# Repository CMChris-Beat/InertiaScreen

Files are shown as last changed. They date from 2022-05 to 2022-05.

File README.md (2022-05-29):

# Inertia Screen 惯性筛

**机电一体化课程设计—惯性筛**

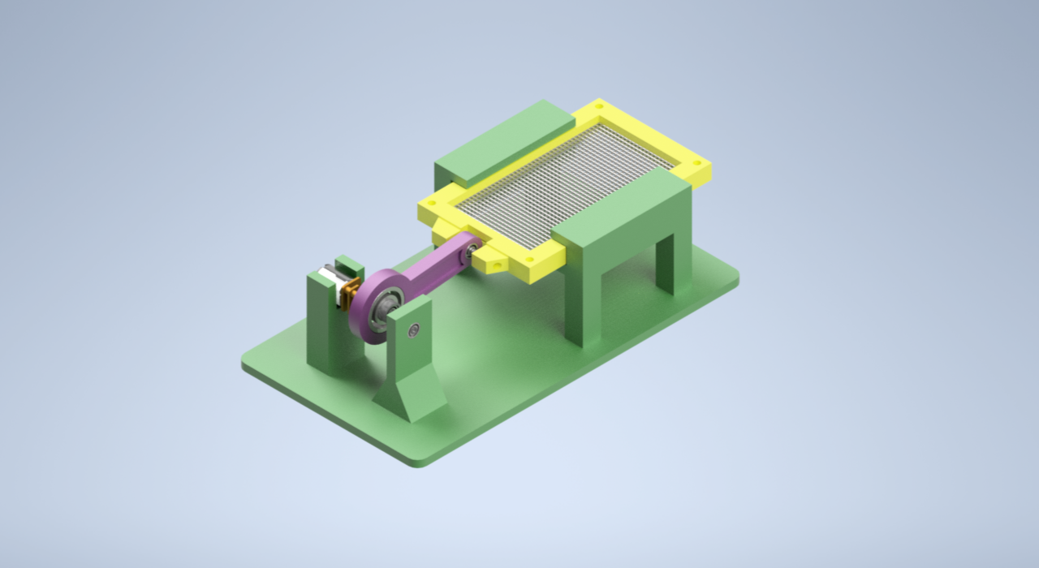
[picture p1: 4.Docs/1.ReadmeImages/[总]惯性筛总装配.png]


> 本项目是为了完成机电一体化课程设计而制作的，在参考了大量的机构后，选择了一个较容易实现且较为美观的设计——偏心轮机构。

另外，在制作完成后发现了一些问题也在这里列举一下：

* **惯性筛的筛动速度问题**，本着节省成本的想法，选用了3.3v~9v 出轴8mm的N20直流电机，但是在使用后一个很明显的问题就是速度，因为自己制作的电路板（V1版本，在更新V2版本的时候忘记备份了。。所以成本上去了，但是V2版本可以做循迹小车，可以遥控的那种）的缘故，电压最高只能给到5V，所以转速基本上是1圈/秒，室友看后直称“老奶奶筛”。˃̣̣̥᷄⌓˂̣̣̥᷅

* **惯性筛的稳定性及配合问题**，所有零件在安装完成后会与仿真图有很大出入，所以在安装的时候尽量保持零件之间的位置关系例如垂直及距离等，尤其是轴和轴配合的同心度也就是零件精度，会直接影响到后面运行时的稳定程度，**电机上方最好也压一下或者胶枪封一下，不然电机会上下跳动。**

* **偏心轮的偏心距问题**，为了制作尺寸小巧，偏心轮的偏心距很小，导致了惯性筛在筛动过程中的动作幅度很小，如果对筛动幅度有要求的化，可以自行加大零件尺寸进行修改。

* **急回特性问题**，本设计中采用的偏心轮可以等价为曲柄滑块机构，而**当偏心轮转动轴与筛网的水平移动轴不共线时，将会出现急回特性**，在本设计中没有考虑该问题，但因为偏心距较小所以急回不明显，但还是希望可以改进并消除该急回特性，保证惯性筛的筛动稳定。

* **惯性筛的效率问题**，制作的实物毕竟只是模型，在**实际筛料的过程中筛网应有一定的倾角**（15°至25°）会使得筛料在筛网上更好的运动，从而让惯性筛的效率提高。

* **零件的打印问题**，其余的都还好，机架长得~~太弯吧~~了，打印的时候加了不少支撑（支撑比模型还坚挺我是真的跪了orz，直接喜提战损版皮肤，~~胶枪粘~~），筛网下方区域是为了**预留空间给收集装置。**

* **一代电路板的问题**，开关的封装用错了导致后来的飞线，在最后我的实物展示图中可以看到，最大的问题是电路板的D7引脚，不知为何，在单独测试过程中输出正常，安装在电路板上时，无论输出高低电平，输出电压都为1.5V造成了很大的问题，我的解决方案是：因为这种结构的惯性筛并不需要正反转控制，所以直接**将D7飞线接地**，就解决了这个问题。

> 建模软件为Inventor而非SolidWorks，是因为我想要向Fusion 360及Inventor建模软件转的缘故，但是我都预留了转换好的Step模型方便大家使用。

> 关于课设要求交的各类文件，我都放在了4.Docs文件夹中，包括了仿真动画、说明书、答辩PPT和电路原理图等也方便大家参考。

---

### 电路部分

关于建模什么的我在这里就不多bb了，会的都会，不会的直接打印。(⁄ ⁄•⁄ω⁄•⁄ ⁄)

而关于电路和程序部分我需要单独讲一下，先是电路，由于操作失误一代也就是我现在使用的并没有保留下来但是原理图还是有的。**原理图中有部分错误已经在上文列出。**

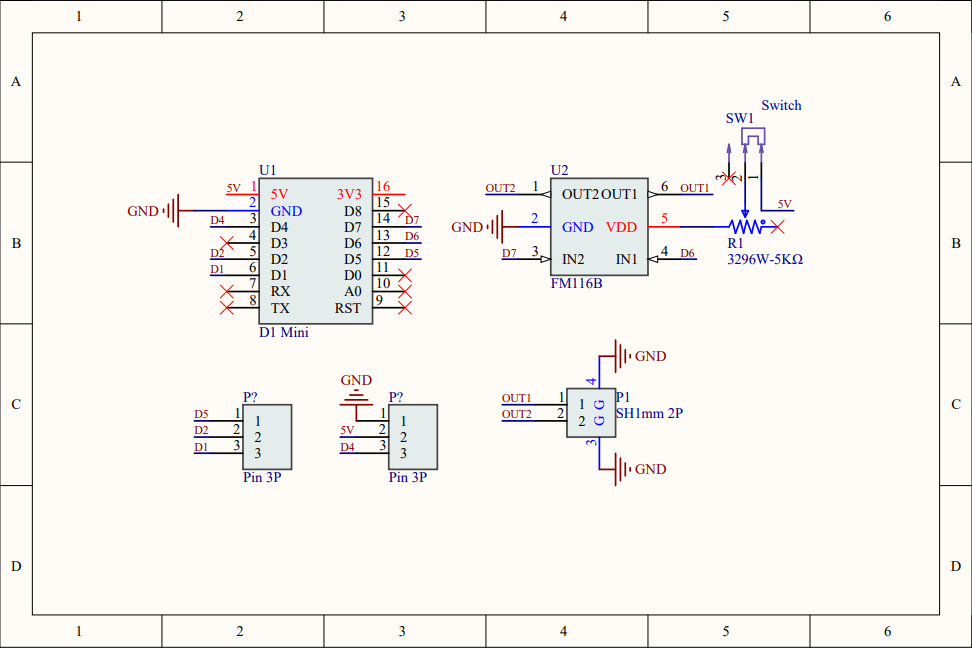
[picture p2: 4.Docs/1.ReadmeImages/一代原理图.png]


> 主要用到的元器件为（元器件皆可在淘宝店铺[优信电子](https://youxin-electronic.taobao.com/shop/view_shop.htm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)买到）：
>
> 1. D1 Mini 开发板（主控）
> 2. SH1.0mm 2P 的插头接口及对应单头线
> 3. FM116B 单路直流电机驱动器
> 4. 滑动变阻器（硬件调速使用）3296W-5KΩ
> 5. 贴片滑动开关
> 6. N20直流减速电机

二代图纸为改进版本，主要为了下学期的课设循迹小车准备的，在制作时同样会开源，可以在我的主页寻找，该电路可以使循迹小车还拥有遥控模式，同样采用N20，运转速度慢，但可以作为小玩具在答辩后玩。

具体的电路元器件需要什么我就不在这里列举了，感兴趣的可以下载后查看。

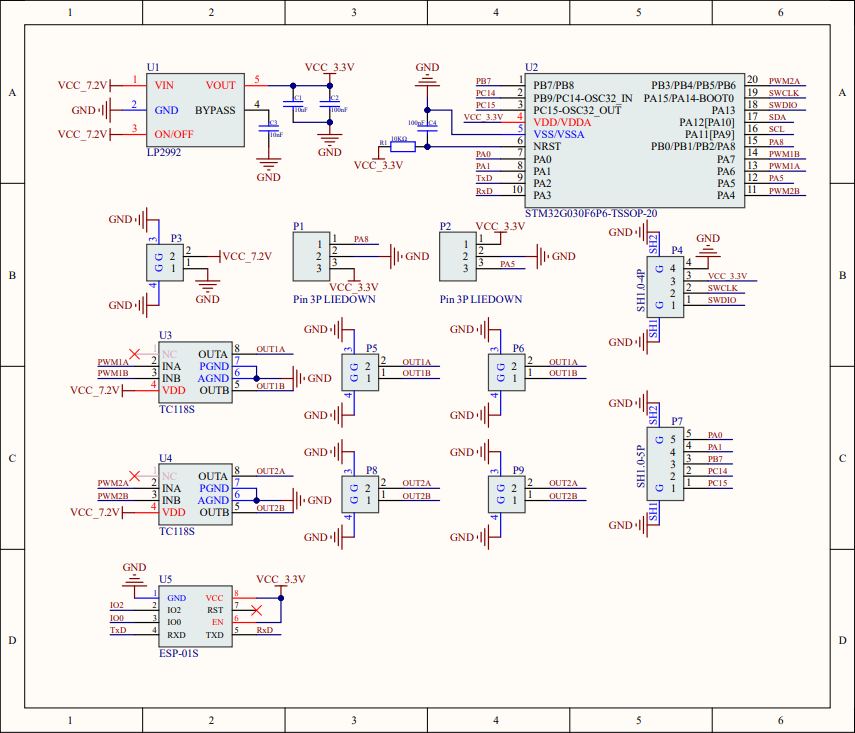
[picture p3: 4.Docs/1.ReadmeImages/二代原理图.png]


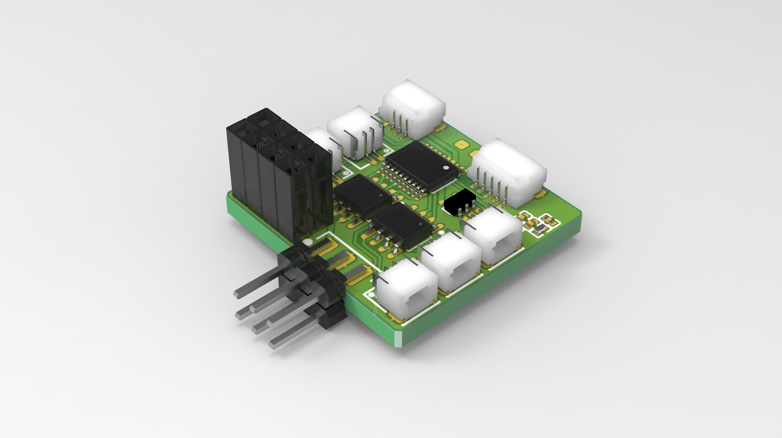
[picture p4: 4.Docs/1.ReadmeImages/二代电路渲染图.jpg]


### 程序部分

程序方面，使用的是Arduino，环境使用的Visual Studio平台下的Visual Micro，也可以使用VS Code的PlatformIO进行开发。

在代码中加入了Blinker库，用于远程手机控制（**点灯Blinker APP**），**要注意将密钥及Wifi等设置为自己的。**

**有能力的小伙伴可以将速度变快变慢的按钮换成滑块，能更好的控制速度，会丝滑很多。**

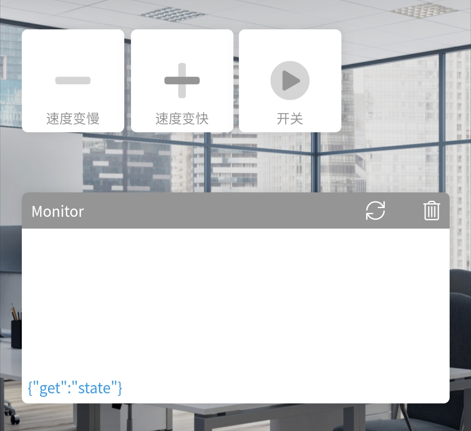
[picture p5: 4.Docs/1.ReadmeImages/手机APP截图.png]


### 实物展示

下面放一下我做好的实物图：



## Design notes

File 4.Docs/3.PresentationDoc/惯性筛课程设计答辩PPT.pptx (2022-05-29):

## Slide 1

机电一体化课程设计
惯性筛

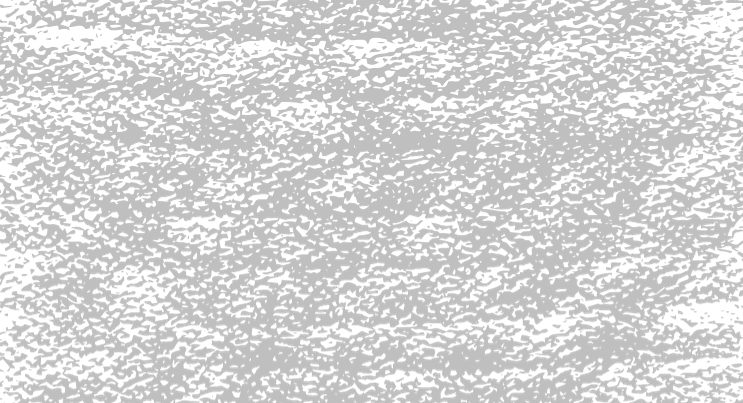
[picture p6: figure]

Course design of Mechatronics—Inertia screen

汇报人：ZHC

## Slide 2

目录
Contents

03.单击文本框输入标题
04.单击文本框输入标题

01.题目分析
02.单击文本框输入标题

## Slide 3

Topic analysis

壹

题目分析

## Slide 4

· 惯性筛是利用物体在没有受到外界作用力下保持静止状态或匀速直线运动状态的性质，来分离不同大小的物体。
· 惯性筛的传动轴在电动机的带动下高速旋转，轴上的圆盘及配重物在旋转过程中产生较大的惯性力，筛子在惯性力的作用下高速来回运动，将中、小物料进行筛分。

工作原理

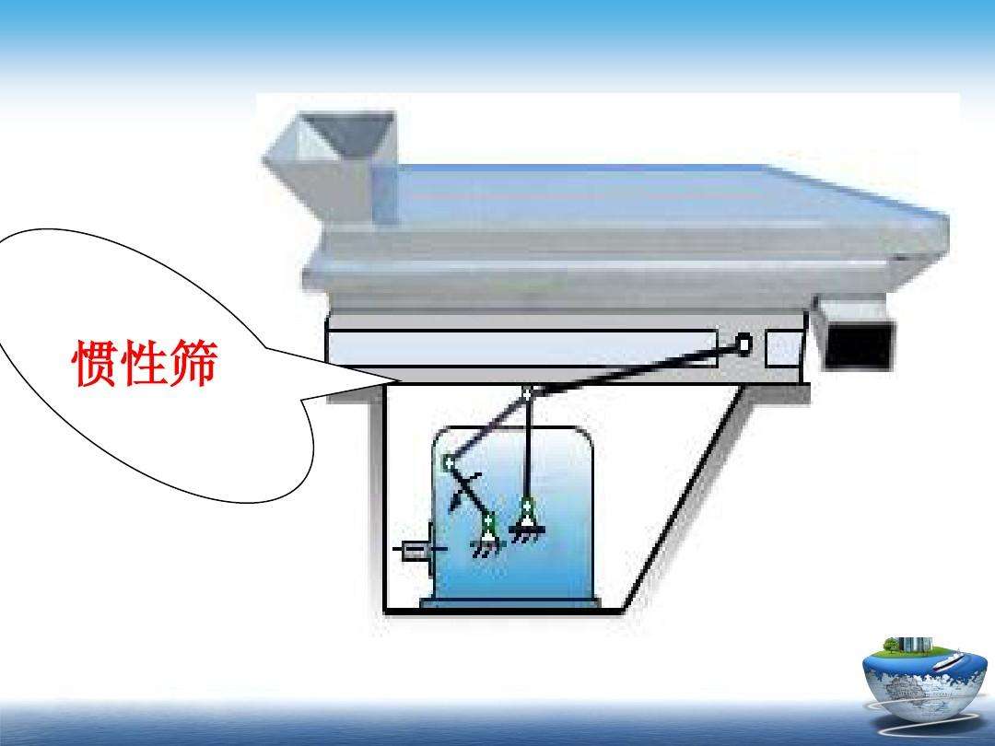
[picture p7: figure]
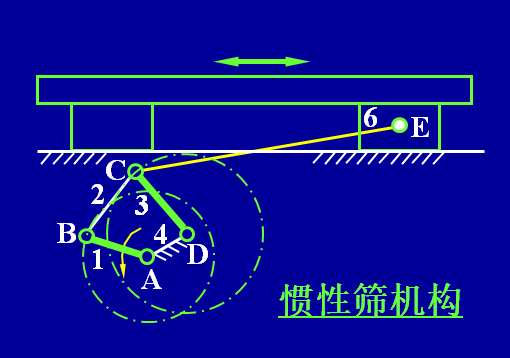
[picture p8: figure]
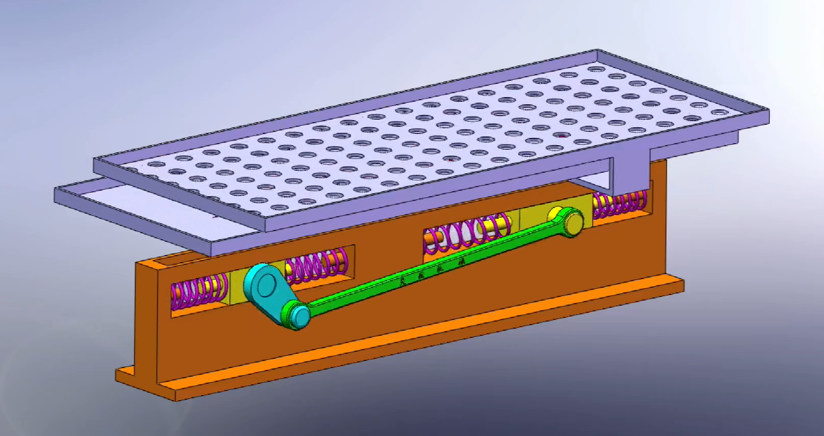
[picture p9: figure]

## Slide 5

传动方案对比

由曲柄和滑块的组合来实现转动和移动相互转换

以曲柄为主动件，把整周转动转换为往复移动

优点：设置为偏置曲柄滑块则具有急回特性

缺点：体积较大

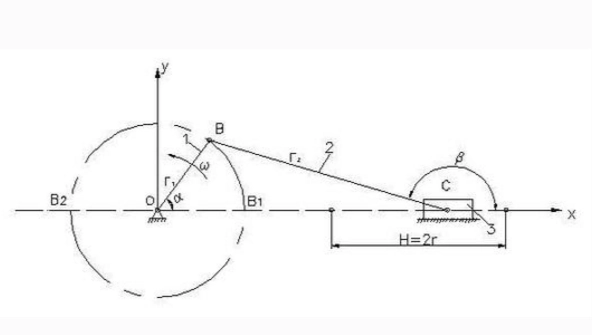
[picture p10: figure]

由凸轮，从动件和机架三个基本构件组成的高副机构

凸轮的轮廓线或凹槽的形状，可将连续的旋转运动转
化为往复的直线运动

优点：运动轨迹可以自行定制

缺点：制造复杂

曲柄滑块机构制作难度中等，采取偏置方式具有急回特性，可以提高运行效率，采取双曲柄带动滑块的方式可以使运行更加简便，也利于安装。

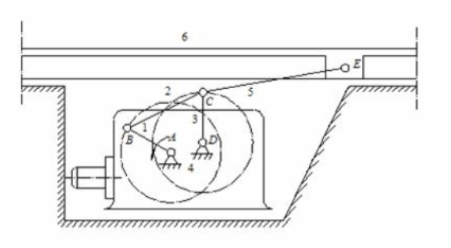
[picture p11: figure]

04
曲柄滑块

02
凸轮机构

03
偏置双曲柄
滑块

01
曲柄摇杆

由一个曲柄和一个摇杆组成的铰链四杆机构

曲柄为主动件且等速转动，而摇杆为从动件作变速往返摆动

优点：制作简单

缺点：输出轨迹不好确定

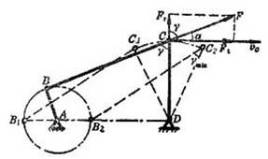
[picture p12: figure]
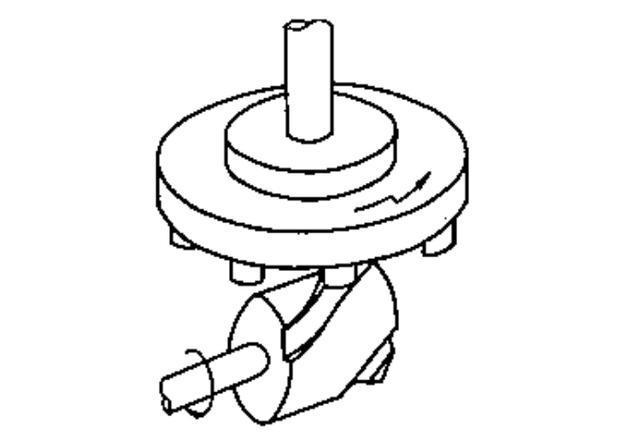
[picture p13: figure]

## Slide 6

传动方案的选择

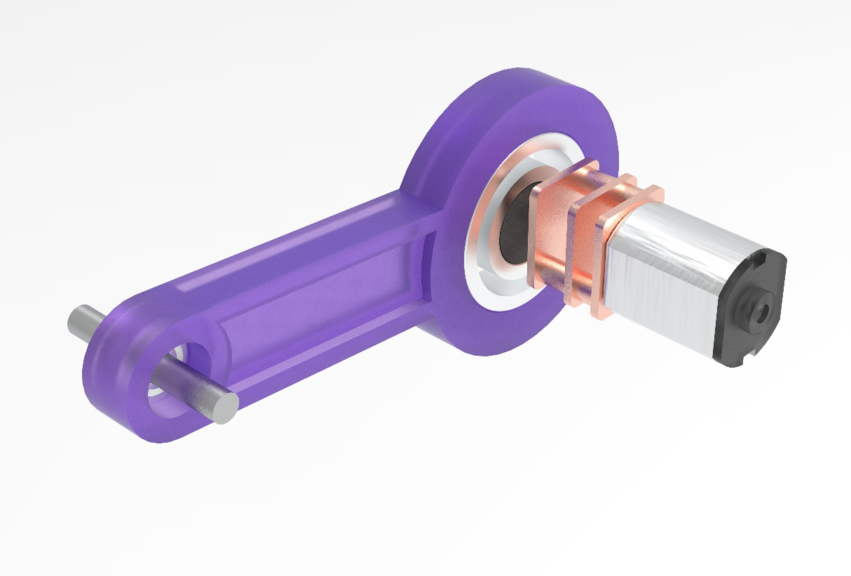
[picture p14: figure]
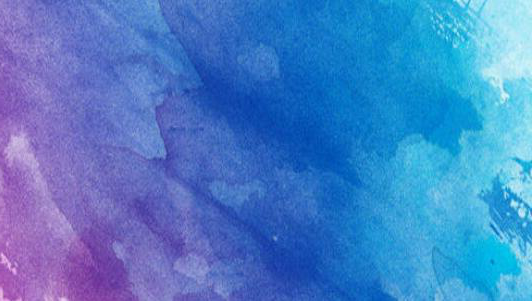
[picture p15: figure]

为了方便制作及体积要小，采用较为简单的结构，曲柄滑块机构，但是两个连杆如果不能保持平面度则不稳定。

使用偏心轮机构将机构简化，增加稳定性的同时，可以使结构变得更加紧凑。

偏心轮机构也有很多形式，为了最简化制作，只是将孔做在一侧，并未使用嵌套形式的偏心轮，固然会损失一部分稳定，但对于模型已经够用了。

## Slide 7

Circuit Design

贰

电路设计

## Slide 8

电路元器件的选择

电机

主控板

接线端子

因为模型较小，采用3D打印的形式进行制作，则电机负载较小，为了减小模型体积选用N20直流减速电机。

在项目初始就想加入联网功能，自然要选择ESP系列，又要求体积较小、好控制，所以选择了D1 Mini板。

为保证传输的稳定性及小型化，采用SH1.0mm封装的端子和插口线。

惯性筛只需要一个电机，为了小型化模型，筛选后采用FM116B单路直流电机驱动芯片进行驱动，成本只有0.7元。

电机驱动

除了能够联网控制外，我们还希望能够通过硬件进行控制，加入了滑动变阻器进行分压调速。

滑动变阻器

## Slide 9

· 电路首先要满足控制需求，由单片机两个IO口对电机驱动FM116B进行控制，因为对转速有调节需求，所以在IO选择上要选择可以输出PWM信号的IO。
· 其次对于滑动变阻器的分压，要注意在电路中的位置，其分压应与驱动芯片进行分压，电机内无电阻，如果在输出端进行分压，则无论阻值大小，所有电压都将由滑动变阻器承担，会导致电机无法转动。
· 为避免后续加入新功能，引出可以使用的几个多余IO口及电源，方便调试。

电路设计

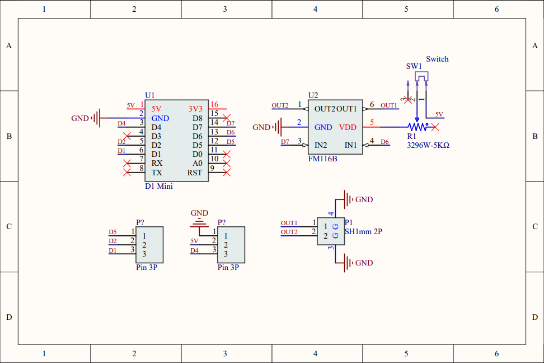
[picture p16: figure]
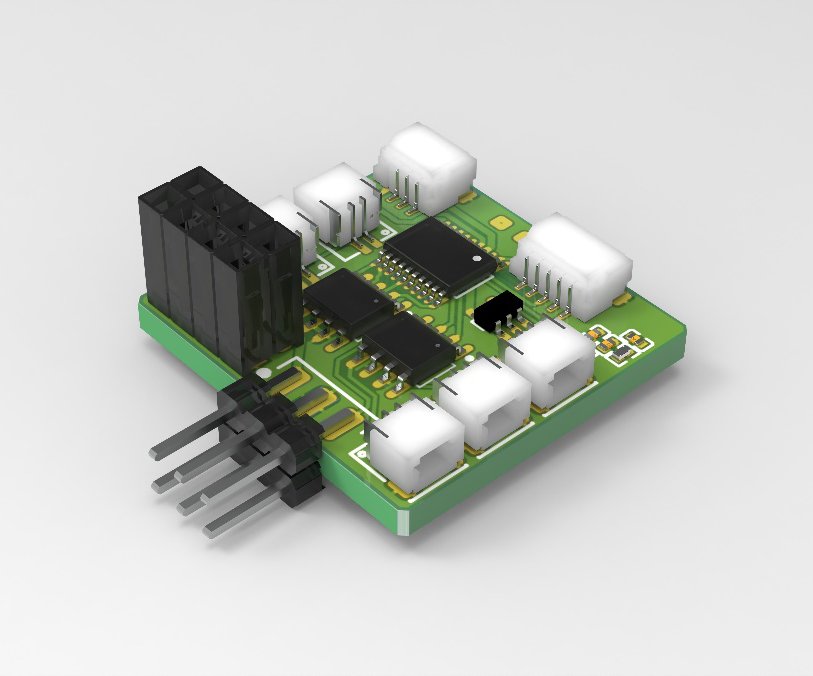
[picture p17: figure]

左上为设计的一代电路板，可以实现基础的功能，但是因为选型等问题出现了很多Bug，所以设计了左侧的二代电路板，加入了很多心得功能，并使其可以完成别的任务，不再局限于只有一个电机的情况。
并且由于一代板子对电机的驱动峰值只有4.6V左右，转速较慢，选用TC118S进行驱动，可以使电机驱动更加细腻。

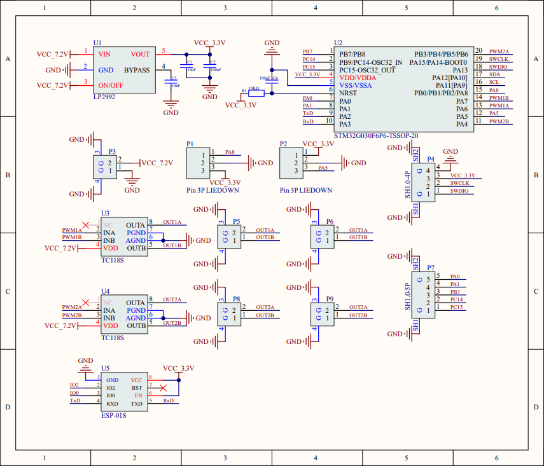
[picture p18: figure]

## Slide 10

Professional Generation Powerpoint

叁

单击文本框输入标题

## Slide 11

传动方案对比

单击编辑标题

单击此处可编辑内容，根据您的需要自由拉伸文本框大小

单击编辑标题

单击此处可编辑内容，根据您的需要自由拉伸文本框大小

单击编辑标题

单击此处可编辑内容，根据您的需要自由拉伸文本框大小

单击编辑标题

单击此处可编辑内容，根据您的需要自由拉伸文本框大小

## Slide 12

单击此处添加标题

单击编辑标题

单击此处可编辑内容，根据您的需要自由拉伸文本框大小

单击编辑标题

单击此处可编辑内容，根据您的需要自由拉伸文本框大小

单击编辑标题

单击此处可编辑内容，根据您的需要自由拉伸文本框大小

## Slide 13

单击此处添加标题

单击编辑标题

单击此处可编辑内容，根据您的需要自由拉伸文本框大小

单击编辑标题

单击此处可编辑内容，根据您的需要自由拉伸文本框大小

单击编辑标题

单击此处可编辑内容，根据您的需要自由拉伸文本框大小

单击编辑标题

单击此处可编辑内容，根据您的需要自由拉伸文本框大小

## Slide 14

单击此处编辑您要的内容，建议您在展示时采用微软雅黑字体，本模版所有图形线条及其相应素材均可自由编辑、改色、替换。更多使用说明和作品请详阅模版最末的使用手册。

单击此处添加标题

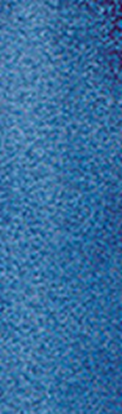
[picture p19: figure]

单击此处可编辑内容，根据您的需要自由拉伸文本框大小

01

单击此处可编辑内容，根据您的需要自由拉伸文本框大小

02

单击此处可编辑内容，根据您的需要自由拉伸文本框大小

03

单击此处可编辑内容，根据您的需要自由拉伸文本框大小

04

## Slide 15

单击此处添加标题

单击此处可编辑内容，根据您的需要自由拉伸文本框大小。单击此处可编辑内容，根据您的需要自由拉伸文本框大小。

关键词

单击此处可编辑内容

关键词

单击此处可编辑内容

关键词

单击此处可编辑内容

关键词

单击此处可编辑内容

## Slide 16

单击此处添加标题

单击编辑标题

单击此处可编辑内容，根据您的需要自由拉伸文本框大小

单击编辑标题

单击此处可编辑内容，根据您的需要自由拉伸文本框大小

单击编辑标题

单击此处可编辑内容，根据您的需要自由拉伸文本框大小

单击编辑标题

单击此处可编辑内容，根据您的需要自由拉伸文本框大小

单击编辑标题

单击此处可编辑内容，根据您的需要自由拉伸文本框大小

单击编辑标题

单击此处可编辑内容，根据您的需要自由拉伸文本框大小

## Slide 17

单击此处添加标题

关键词

1

单击此处编辑您要的内容，建议您在展示时采用微软雅黑字体。

关键词

2

单击此处编辑您要的内容，建议您在展示时采用微软雅黑字体。

关键词

单击此处编辑您要的内容，建议您在展示时采用微软雅黑字体。

3

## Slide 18

单击此处添加标题

单击编辑标题

单击此处可编辑内容，根据您的需要自由拉伸文本框大小

01

关键词

02

关键词

单击编辑标题

单击此处可编辑内容，根据您的需要自由拉伸文本框大小

03

关键词

04

关键词

单击编辑标题

单击此处可编辑内容，根据您的需要自由拉伸文本框大小

单击编辑标题

单击此处可编辑内容，根据您的需要自由拉伸文本框大小

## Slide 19

单击此处添加标题

单击此处可编辑内容，根据您的需要自由拉伸文本框大小

关键词

关键词

单击此处可编辑内容，根据您的需要自由拉伸文本框大小

单击此处可编辑内容，根据您的需要自由拉伸文本框大小

单击此处可编辑内容，根据您的需要自由拉伸文本框大小

关键词

关键词

单击此处可编辑内容，根据您的需要自由拉伸文本框大小

关键词

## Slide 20

单击此处添加标题

W
26%

S
85%

T
10%

O
45 %

单击编辑标题

单击此处可编辑内容，根据您的需要自由拉伸文本框大小

单击编辑标题

单击此处可编辑内容，根据您的需要自由拉伸文本框大小

单击编辑标题

单击此处可编辑内容，根据您的需要自由拉伸文本框大小

单击编辑标题

单击此处可编辑内容，根据您的需要自由拉伸文本框大小

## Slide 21

单击此处添加标题

单击此处可编辑内容，根据您的需要自由拉伸文本

单击此处可编辑内容，根据您的需要自由拉伸文本

关键词

关键词

关键词

单击此处可编辑内容，根据您的需要自由拉伸文本

单击此处可编辑内容，根据您的需要自由拉伸文本

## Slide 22

Professional Generation Powerpoint

肆

单击文本框输入标题

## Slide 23

单击此处添加标题

单击编辑标题

单击此处可编辑内容，根据您的需要自由拉伸文本框大小

单击编辑标题

单击此处可编辑内容，根据您的需要自由拉伸文本框大小

单击编辑标题

单击此处可编辑内容，根据您的需要自由拉伸文本框大小

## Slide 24

单击此处编辑您要的内容，建议您在展示时采用微软雅黑字体，本模版所有图形线条及其相应素材均可自由编辑、改色替换。更多使用说明和作品请详阅模版最末的使用手册。

单击此处添加标题

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
单击编辑标题

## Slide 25

单击此处添加标题

本模板的所有素材和逻辑图表，均可自由编辑替换和移动。

本模板的所有素材和逻辑图表，均可自由编辑替换和移动。

本模板的所有素材和逻辑图表，均可自由编辑替换和移动。

本模板的所有素材和逻辑图表，均可自由编辑替换和移动。

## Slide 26

单击此处添加标题

单击编辑标题

单击此处可编辑内容，根据您的需要自由拉伸文本框大小

单击编辑标题

单击此处可编辑内容，根据您的需要自由拉伸文本框大小

单击编辑标题

单击此处可编辑内容，根据您的需要自由拉伸文本框大小

单击编辑标题

单击此处可编辑内容，根据您的需要自由拉伸文本框大小

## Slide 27

THANK YOU

谢谢您的聆听

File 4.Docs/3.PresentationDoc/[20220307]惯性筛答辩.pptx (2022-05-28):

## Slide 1

惯性筛
课程设计

答辩人姓名

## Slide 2

CONTENTS

题目分析

01

工作原理及组成

02

传动方案对比与选择

03

总结

04

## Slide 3

01

题目分析

利用物体在没有受到外界作用力下保持静止状态或匀速直线运动状态的性质，来分离不同大小的物体。

体积大

筛网

惯性筛

体积小

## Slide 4


5、轴承
6、传动机构等

01

工作原理

惯性筛的传动轴在电动机的带动下高速旋转，轴上的圆盘及配重物在旋转过程中产生较大的惯性力，筛子在惯性力的作用下高速来回运动，将中、小物料进行筛分。

02

组成

1、筛箱
2、筛网
3、传动轴
4、电动机

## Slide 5

传动方案的对比与选择

曲柄滑块机构

曲柄摇杆机构

1

2

3

4

偏置双曲柄
滑块机构

凸轮机构

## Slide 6

传动方案的对比与选择


曲柄滑块机构

由曲柄和滑块的组合来实现转动和移动相互转换

以曲柄为主动件，把整周转动转换为往复移动

优点：设置为偏置曲柄滑块则具有急回特性

缺点：体积较大

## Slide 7

传动方案的对比与选择


凸轮机构

由凸轮，从动件和机架三个基本构件组成的高副机构

凸轮的轮廓线或凹槽的形状，可将连续的旋转运动转
化为往复的直线运动

优点：运动轨迹可以自行定制

缺点：制造复杂

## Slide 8

传动方案的对比与选择


曲柄摇杆机构

由一个曲柄和一个摇杆组成的铰链四杆机构

曲柄为主动件且等速转动，而摇杆为从动件作变速往返摆动

优点：制作简单

缺点：输出轨迹不好确定

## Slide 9

总结

偏置双曲柄滑块机构


曲柄滑块机构制作难度中等，采取偏置方式具有急回特性，可以提高运行效率，采取双曲柄带动滑块的方式可以使运行更加简便，也利于安装。

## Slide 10

THANKS

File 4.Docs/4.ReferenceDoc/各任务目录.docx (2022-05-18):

第八章 平面连杆机构及其设计.ppt

曲柄摇杆装置：

1) 曲柄摇杆机构
2) 曲柄摇杆1 、
3) 曲柄摇杆2 、
4) 双曲柄、
5) 双摇杆机构
6) 雷达天线俯仰机构 曲柄主动 曲柄摇杆机构演化

7）缝纫机踏板机构 摇杆主动

8）惯性筛机构 双曲柄机构演化

9）车门开闭机构 反平行四边形机构

10）汽车转向机构 等腰梯形机构 双摇杆机构

11）曲柄滑块机构

12) 小型刨床 导杆机构

13) 牛头刨床 导杆机构

14) 手摇唧筒

15) 正弦机构

16)圆盘锯

17）绕线机模型

18）对心直动滚子凸轮模型

19）内燃机气门机构模型

20）输送机模型

21）自动搬运小车

22）两级齿轮传动模型

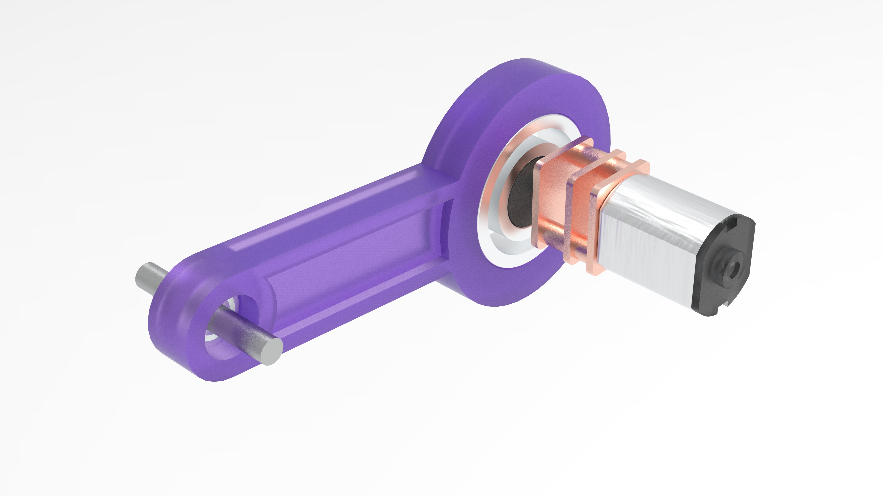
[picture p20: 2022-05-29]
4.Docs/1.ReadmeImages/偏心轮机构.jpg

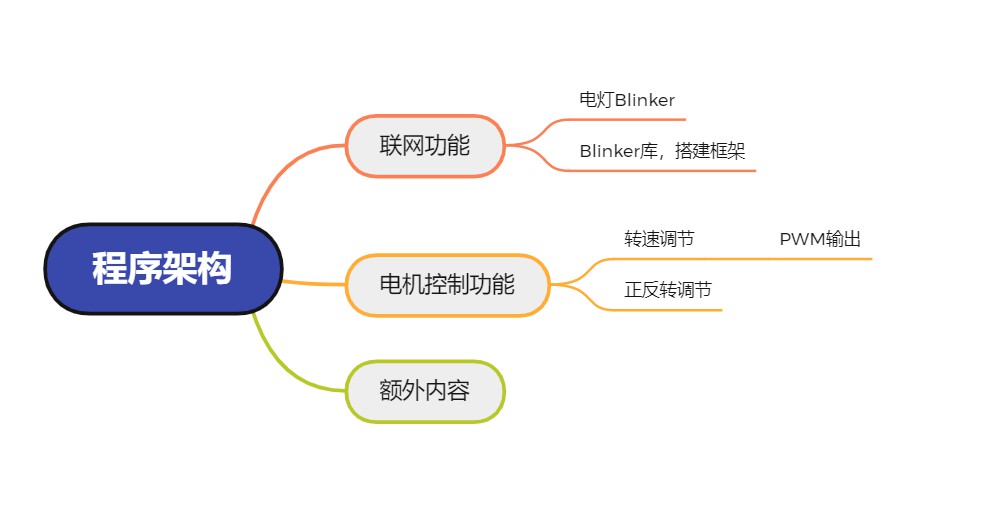
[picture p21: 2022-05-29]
4.Docs/1.ReadmeImages/程序框架.jpg

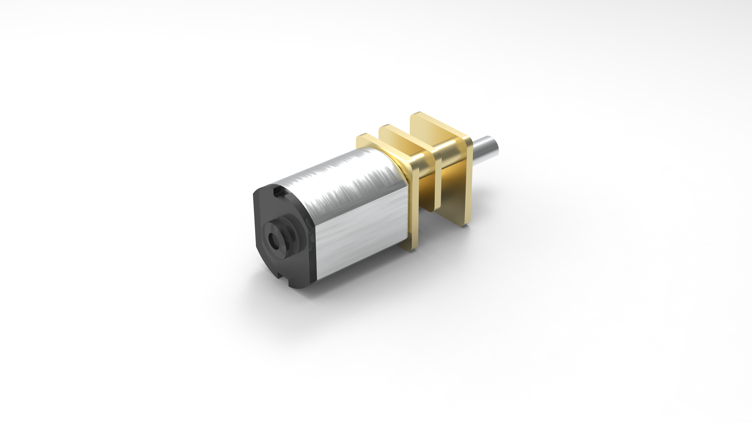
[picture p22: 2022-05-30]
4.Docs/1.ReadmeImages/N20电机渲染.jpg

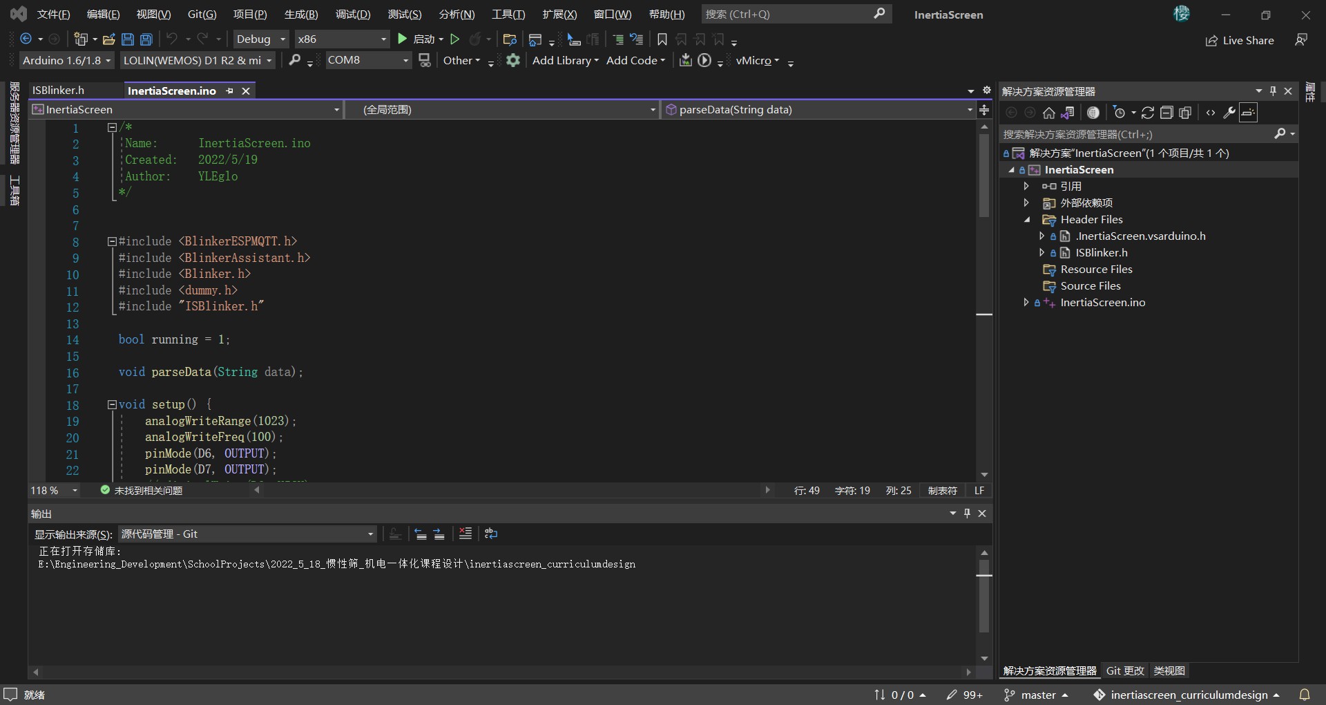
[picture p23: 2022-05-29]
4.Docs/1.ReadmeImages/程序截图.jpg

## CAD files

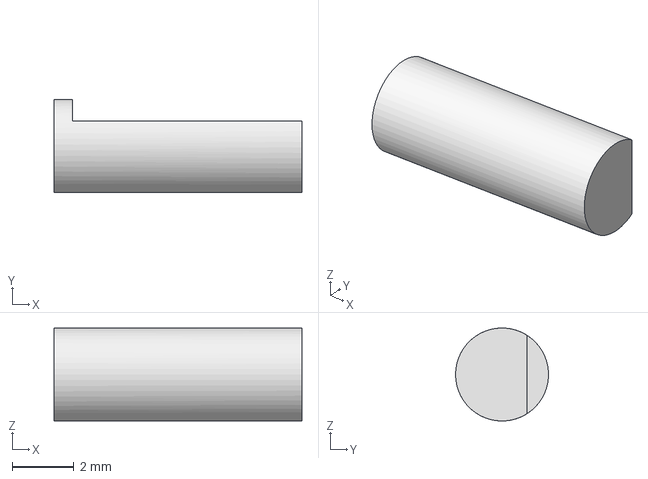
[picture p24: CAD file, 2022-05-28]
3.Model/2.3D_Simulation/Step/GA12-N20微型减速直流电机转动轴.stp
8.00 x 3.00 x 3.00 mm

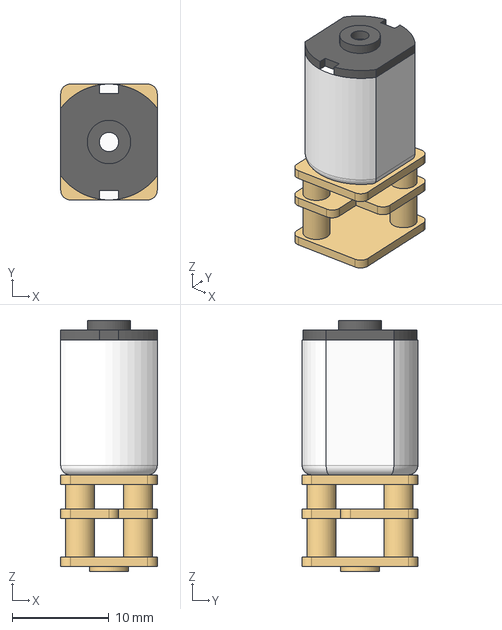
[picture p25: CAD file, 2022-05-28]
3.Model/2.3D_Simulation/Step/GA12-N20微型减速直流电机主机.stp
10.0 x 12.0 x 26.0 mm

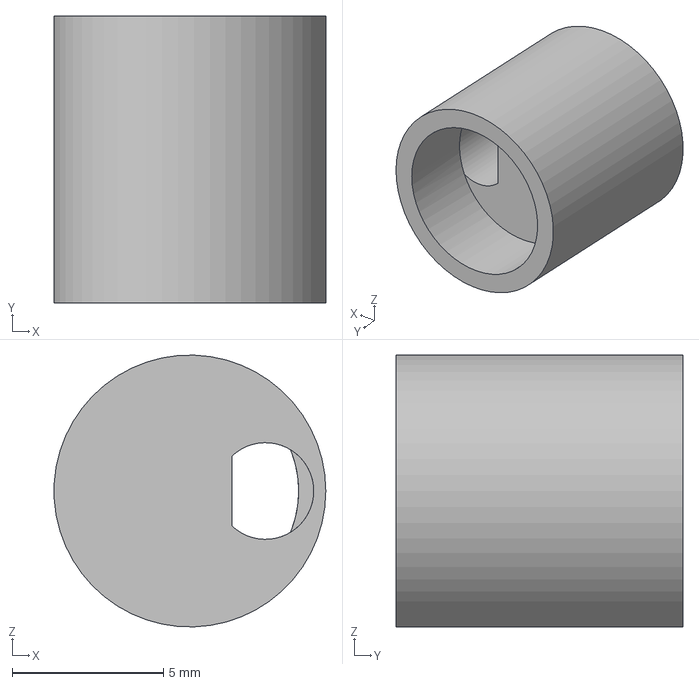
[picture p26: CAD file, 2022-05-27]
3.Model/2.3D_Simulation/Step/偏心轮.stp
8.99 x 9.50 x 9.00 mm

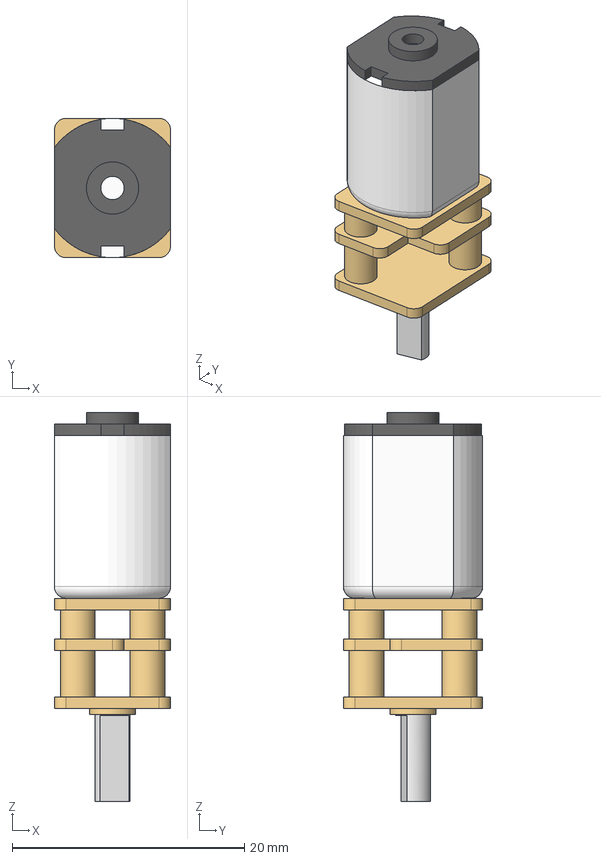
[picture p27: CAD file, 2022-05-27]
3.Model/2.3D_Simulation/Step/GA12-N20微型减速直流电机3V_15RPM_8mm.stp
10.0 x 12.0 x 33.5 mm
GA12-N20微型减速直流电机3V_15RP M
GA12-N20微型减速直流电机转动轴

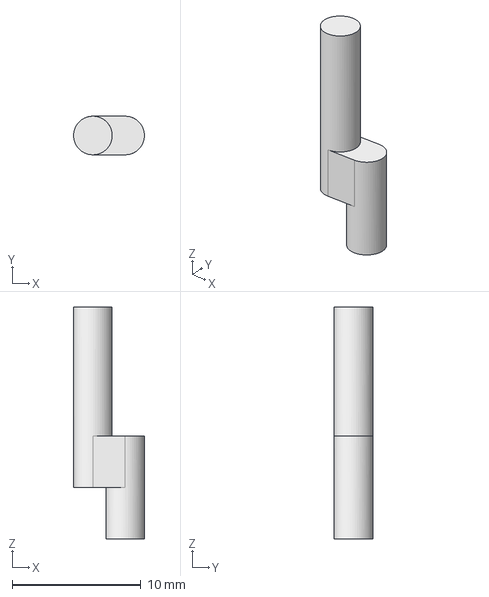
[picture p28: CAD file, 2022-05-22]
3.Model/2.3D_Simulation/Step/偏心支轴.stp
5.50 x 3.00 x 18.0 mm

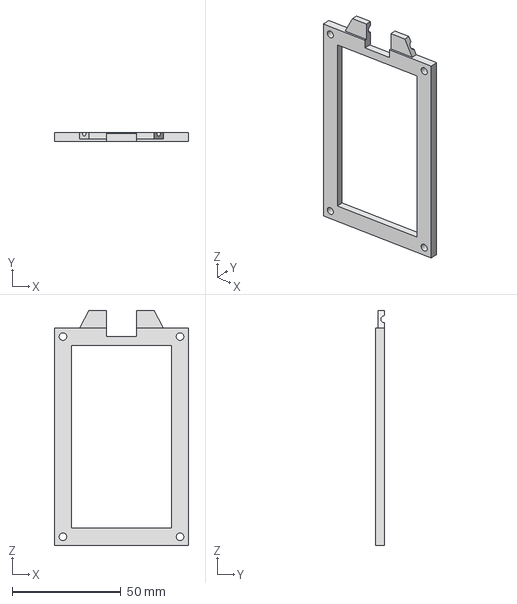
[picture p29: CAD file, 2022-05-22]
3.Model/2.3D_Simulation/Step/筛网上.stp
61.8 x 4.00 x 108.0 mm

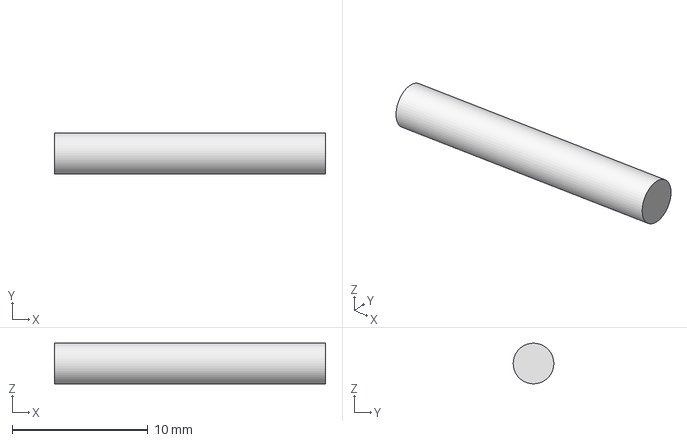
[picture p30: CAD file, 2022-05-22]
3.Model/2.3D_Simulation/Step/轴.stp
20.0 x 3.00 x 3.00 mm

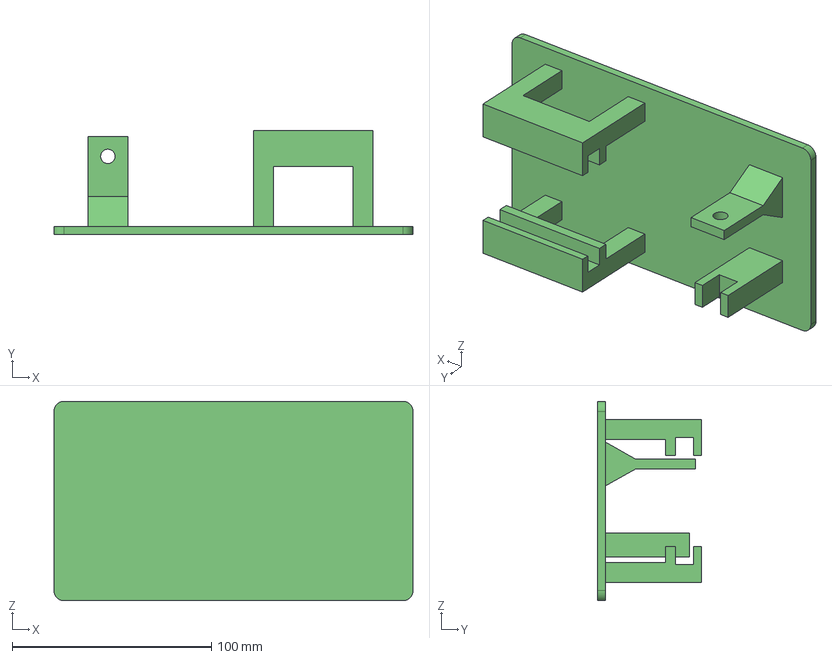
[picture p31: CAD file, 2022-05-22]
3.Model/2.3D_Simulation/Step/机架.stp
180.0 x 52.0 x 100.0 mm

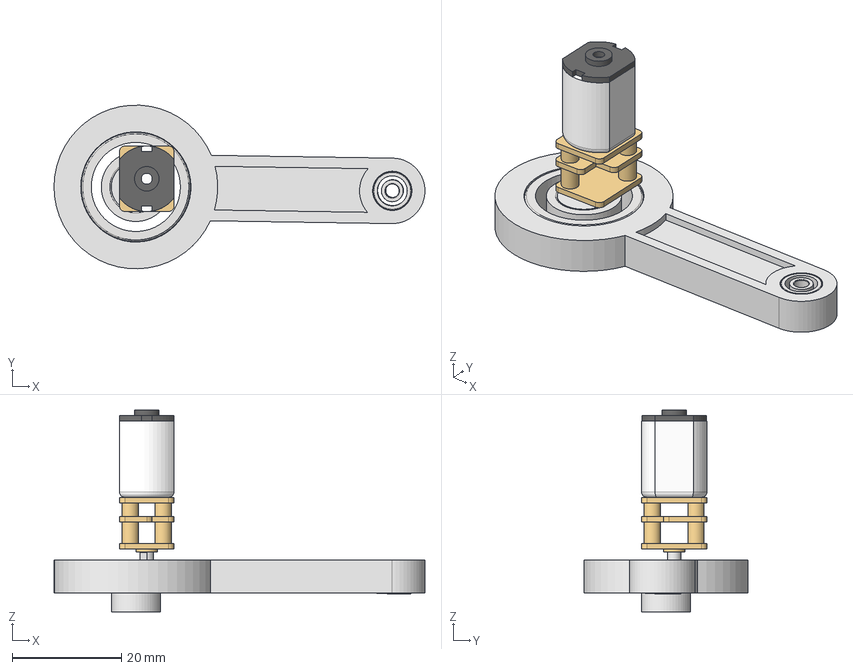
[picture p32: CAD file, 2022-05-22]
3.Model/2.3D_Simulation/Step/[装配]惯性筛偏心轮装配.stp
68.0 x 30.0 x 37.0 mm
GA12-N20微型减速直流电机3V_15RP M
GA12-N20微型减速直流电机转动轴
偏心轮
偏心轮外连接件
ISO 1224 - 38 3 x 7 x 3
ISO 1224 - 19 9 x 20 x 6
ISO 1224 - 19 2.5 x 7 x 2.5 x 2

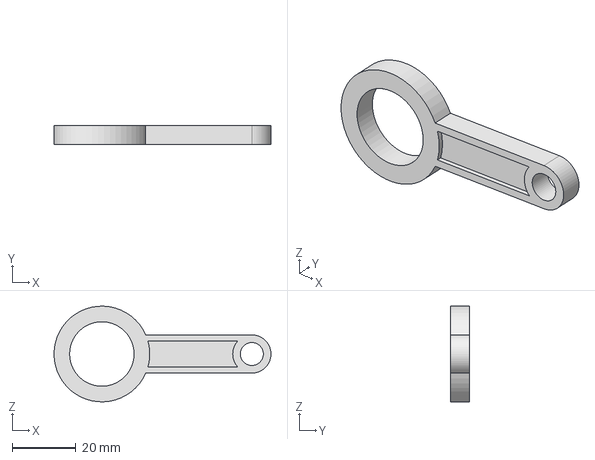
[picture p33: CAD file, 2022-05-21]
3.Model/2.3D_Simulation/Step/偏心轮外连接件.stp
68.0 x 6.00 x 30.0 mm

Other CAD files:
3.Model/1.Drawings/惯性筛装配图.dwg
3.Model/1.Drawings/筛网上.dwg
3.Model/1.Drawings/筛网下.dwg
3.Model/1.Drawings/偏心轮.dwg
3.Model/1.Drawings/偏心轮外连接件.dwg
3.Model/1.Drawings/机架.dwg
3.Model/1.Drawings/偏心支轴.dwg
3.Model/2.3D_Simulation/Step/筛网下.stp
3.Model/2.3D_Simulation/Ipt/1.偏心轮/GA12-N20微型减速直流电机3V_15RPM_8mm.iam
3.Model/2.3D_Simulation/Ipt/1.偏心轮/GA12-N20微型减速直流电机3V_15RPM_8mm.ipt
3.Model/2.3D_Simulation/Ipt/1.偏心轮/GA12-N20微型减速直流电机主机.ipt
3.Model/2.3D_Simulation/Ipt/1.偏心轮/GA12-N20微型减速直流电机转动轴.ipt
3.Model/2.3D_Simulation/Ipt/1.偏心轮/偏心支轴.ipt
3.Model/2.3D_Simulation/Ipt/1.偏心轮/偏心轮.ipt
3.Model/2.3D_Simulation/Ipt/1.偏心轮/偏心轮外连接件.ipt
3.Model/2.3D_Simulation/Ipt/2.轴承/BS 3469 - 19 - 2.5 x 7 x 2.5.ipt
3.Model/2.3D_Simulation/Ipt/2.轴承/ISO 1224 - 19 2.5 x 7 x 2.5.ipt
3.Model/2.3D_Simulation/Ipt/2.轴承/ISO 1224 - 19 9 x 20 x 6.ipt
3.Model/2.3D_Simulation/Ipt/2.轴承/ISO 1224 - 38 3 x 7 x 3.ipt
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

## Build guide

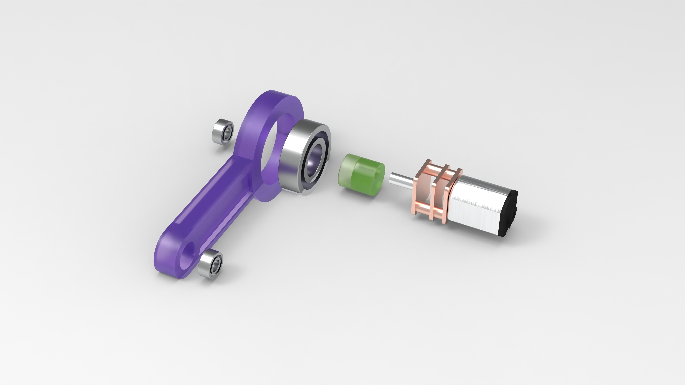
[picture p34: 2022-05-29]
4.Docs/1.ReadmeImages/偏心轮机构组装图.jpg

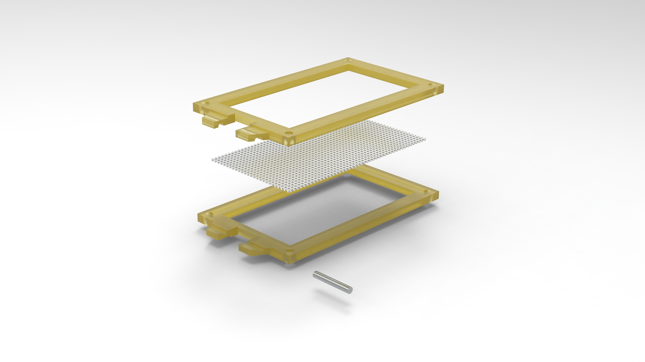
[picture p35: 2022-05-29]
4.Docs/1.ReadmeImages/筛网组装图.jpg

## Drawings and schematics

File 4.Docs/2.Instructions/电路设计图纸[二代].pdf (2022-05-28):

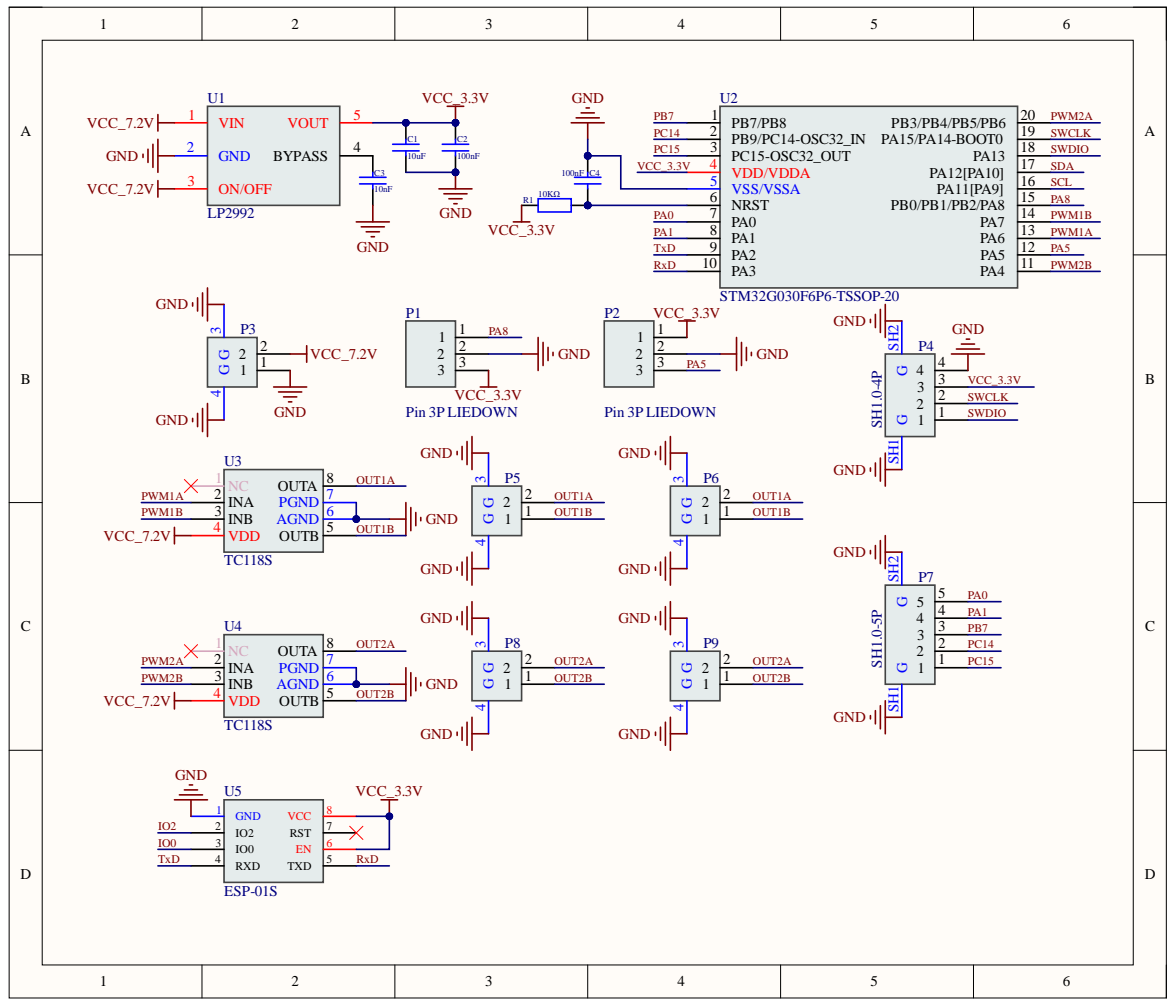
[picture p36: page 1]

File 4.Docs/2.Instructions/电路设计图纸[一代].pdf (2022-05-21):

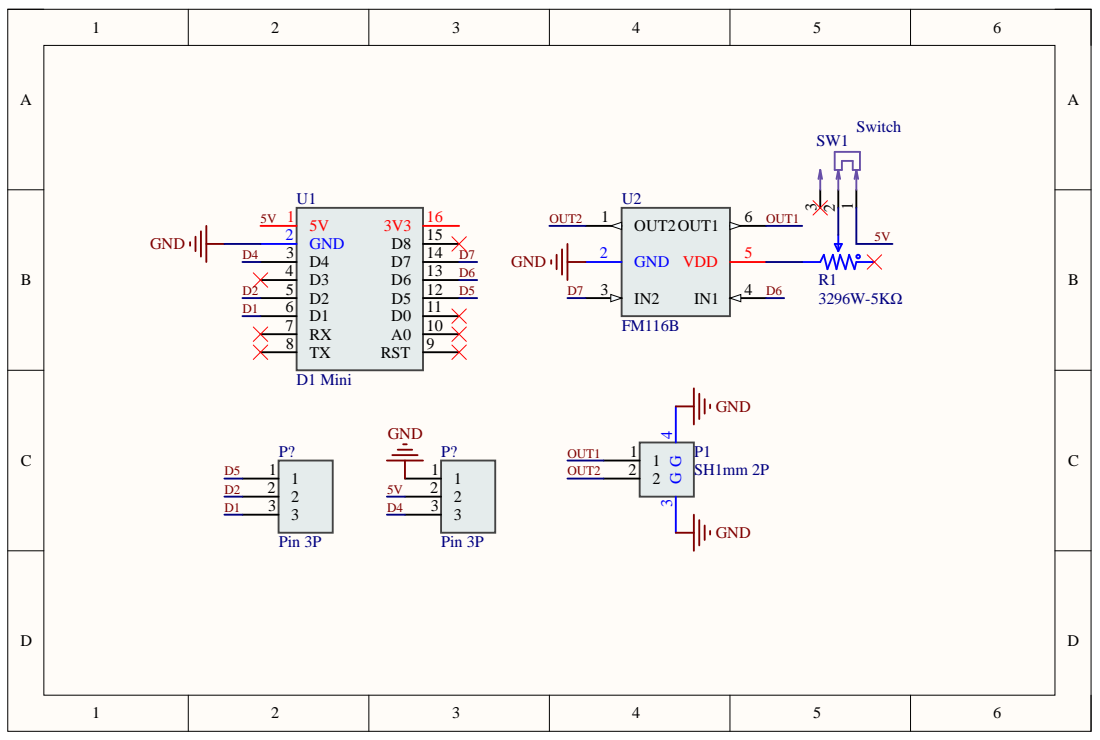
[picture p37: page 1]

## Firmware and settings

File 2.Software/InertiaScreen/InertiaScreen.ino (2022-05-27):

/*
 Name:		InertiaScreen.ino
 Created:	2022/5/19
 Author:	YLEglo
*/


#include <BlinkerESPMQTT.h>
#include <BlinkerAssistant.h>
#include <Blinker.h>
#include <dummy.h>
#include "ISBlinker.h"

bool running = 1;

void parseData(String data);

void setup() {
	analogWriteRange(1023);
	analogWriteFreq(100);
	pinMode(D6, OUTPUT);
	pinMode(D7, OUTPUT);
	// digitalWrite(D6, HIGH);
	analogWrite(D6, speed);
	digitalWrite(D7, LOW);
	BLINKER_DEBUG.stream(Serial);
	Blinker.begin(auth, ssid, pswd);
	Button1.attach(button1_callback);
	Button2.attach(button2_callback);
	Button3.attach(button3_callback);
}

void loop() {
	Blinker.run();
	parseData(input);
	if (running == 0) analogWrite(D6, 0);
	else analogWrite(D6, speed);
}

void parseData(String data) {
	switch (data.toInt()) {
		case 1: // Slow
			if (flag) {
				if (speed > 23) speed -= 100;
				Blinker.print("Speed: ", speed);
				flag = 0;
			}
			break;
		case 2: // Quick
			if (flag) {
				if (speed < 1023) speed += 100;
				Blinker.print("Speed: ", speed);
				flag = 0;
			}
			break;
		case 3: // Stop
			if (flag) {
				running = !running;
				Blinker.print("State: ", running);
				flag = 0;
			}
			break;
		default:
			running = 1;
			break;
	}
}

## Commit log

2022-05-18 [HW]Upload Hardware Project
    [InertiaScreen_CurriculumDesign.PcbDoc, InertiaScreen_CurriculumDesign.PrjPcb, InertiaScreen_CurriculumDesign.SchDoc]
2022-05-18 [Md]Upload part of Model
    [InertiaScreen_CurriculumDesign.SchDoc, 偏心轮.ipt]
2022-05-19 [SW]Upload Test Program
    [InertiaScreen_CurriculumDesign.PrjPcb, InertiaScreen_CurriculumDesign.SchDoc, 偏心轮.0001.ipt]
2022-05-20 [HW]Update Hardware
    [InertiaScreen_CurriculumDesign.PcbDoc, InertiaScreen_CurriculumDesign.SchDoc]
2022-05-21 [Docs]Upload Circuit Drawing
    [InertiaScreen_CurriculumDesign.PrjPcb, InertiaScreen_CurriculumDesign.SchDoc]
2022-05-21 [Md]Update Model, complete Eccentric mechanism
    [BS 3469 - 19 - 2.5 x 7 x 2.5.ipt, GA12-N20微型减速直流电机3V_15RPM_8mm.ipt, GA12-N20微型减速直流电机3V_15RPM_8mm.stp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]
2022-05-21 Organize documents
    [BS 3469 - 19 - 2.5 x 7 x 2.5.ipt, GA12-N20微型减速直流电机3V_15RPM_8mm.ipt, ISO 1224 - 19 2.5 x 7 x 2.5.ipt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]
2022-05-21 [Md]Update Model, only Rack left
    [GA12-N20微型减速直流电机3V_15RPM_8mm.iam, GA12-N20微型减速直流电机3V_15RPM_8mm.ipt, GA12-N20微型减速直流电机主机.ipt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]
2022-05-22 [Md]Complete Model making
    [GA12-N20微型减速直流电机3V_15RPM_8mm.iam, GA12-N20微型减速直流电机3V_15RPM_8mm.stp, [总]惯性筛总装配.iam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]
2022-05-22 [Md]Upload 2D drawing
    [[总]惯性筛总装配.iam, 偏心支轴.dwg, 偏心轮.dwg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]
2022-05-25 [HW]Update Hardware, Replace the switch package
    [InertiaScreen_CurriculumDesign.PcbDoc, InertiaScreen_CurriculumDesign.SchDoc]
2022-05-27 [HW]Update Hardware and revise some 3D Model
    [GA12-N20微型减速直流电机3V_15RPM_8mm.iam, GA12-N20微型减速直流电机3V_15RPM_8mm.ipt, GA12-N20微型减速直流电机3V_15RPM_8mm.stp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]
2022-05-28 Overall optimization, Update Readme
    [GA12-N20微型减速直流电机主机.stp, GA12-N20微型减速直流电机转动轴.stp, ISO 1224 - 19 9 x 20 x 6.stp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]
2022-05-28 [Md]Update 2D Drawings
    [惯性筛装配图.dwg]
2022-05-29 [Docs]Update PPT(NV)
    [InertiaScreen_CurriculumDesign.PcbDoc]
2022-05-30 删除 惯性筛设计说明书.pdf
